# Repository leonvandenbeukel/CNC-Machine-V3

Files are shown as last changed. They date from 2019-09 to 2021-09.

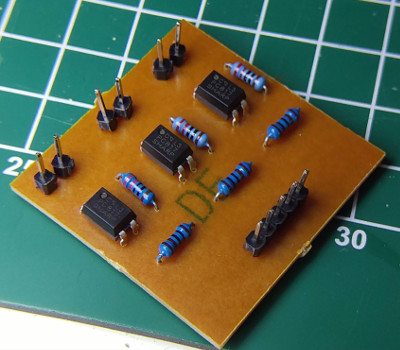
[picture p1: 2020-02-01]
Image/pcb3.jpg

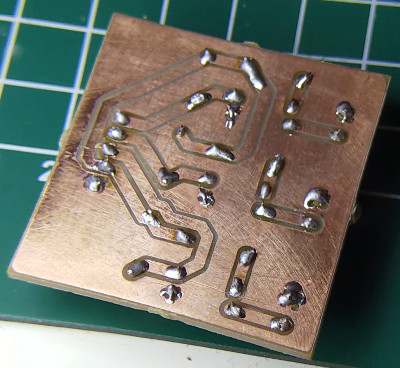
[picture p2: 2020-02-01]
Image/pcb2.jpg

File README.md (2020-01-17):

# CNC Machine V3
 
### Warning and disclaimer

Just as mentioned with my previous version, if you want to build this machine yourself you can download all the necessary files but I don't have enough time to give you much support so build it at your own risk! Also always be very careful with powertools, and only use them if you know what you're doing. 

### Wiki

Check out the [Wiki](https://github.com/leonvandenbeukel/CNC-Machine-V3/wiki) for specific milling info and parameter settings.

### License

<br />This work is licensed under a <a rel="license" href="http://creativecommons.org/licenses/by-nc-sa/4.0/">Creative Commons Attribution-NonCommercial-ShareAlike 4.0 International License</a>.

If you have any suggestions on how to make the machine better, please let me know!

### Introduction
 
This is a modified version of my previous homemade CNC machine. Instead of using threaded rods this one uses (GT2) belts and has a larger working area of 50x70 cm or 20x27 inch. By using belts it's also faster. I'm also using microstepping now (all three jumpers) on the Arduino CNC shield. The STL files for 3D printing can be found in the STL folder. 

The metal tubes are 20x20mm and approx. 1 meter long (X axis is a little shorter). 

### Design

I've designed the 3D printed parts with Fusion 360 and used Inkscape for the Y axis drilling template. To control the machine I'm using an Arduino UNO with GRBL firmware and an Arduino CNC Shield. There are plenty of tutorials to find on how to connect and use it so I did not show it in the video. Here are some useful links:

* [GRBL](https://github.com/gnea/grbl)
* [Arduino CNC Shield](https://blog.protoneer.co.nz/arduino-cnc-shield/)

### 3D Printing

The 3D printer I use is an Anet A8. The parts are printed with PLA, mostly 20% infill and 0.2 or 0.4 setting. Use higher infill for parts that must be stronger, for example the stepper motor mounts.

| 3D Printed components | x Print |
| --- | ----- |
|Bearing Belt Guidener | 6x |
|Router Mount | 1x |
|Universal Mount | 4x |
|X Axis Belt Holder | 4x |
|X Axis Motor Mount | 1x |
|X Axis Sidepanel Mount Inside  | 2x |
|X Axis Sidepanel Mount Outside | 2x |
|X Axis Spacer | 2x |
|Y Axis Motor Mount and Slider  | 2x |
|Y Mount | 4x |
|Z Axis Bottom Front | 1x |
|Z Axis Top Front | 1x |
|Z Carriage Back | 1x |
|Z Carriage Top | 1x |
|Z Motor Mount | 1x |
|Z Slider Bottom | 1x |
|Z Slider Top | 1x |
|Z Spacer | 1x |

### Dimensions

The tubes are 20mm x 20mm (0.78") square steel tubes. The length of the Y Axis tubes is 1000mm (40") and the length for the X Axis is approx. 820mm (32"). As an alternative you could also use other dimensions than 20mm x 20mm (maybe even rounded tubes) as long as they are approximately that size. The Z axis tubes are 15mm x 15mm (0.59") aluminium square tubes, approx. 215mm long (8.5"). You should measure this for yourself, check the video build. For the belts I'm using GT2 6mm and pulleys.

The effective working area is 50 x 70 cm (20" x 27").

### Power and motors

To power the NEMA 17 stepper motors I've converted an old ATX PC power supply and used the 12V output. The type of stepper motors I use for the Y- and Z axis are: 17HS19-2004S1, the type for the X axis is: 42BYGHW811. Both type of motors can be used. For the wiring I've used CAT5 network cable.

### Cost Estimation

* [Link to Google Sheet](https://docs.google.com/spreadsheets/d/1WaLTZEe9Un130kNA_mwn08Lo0E_RAs8ju6dJp0eKexQ/edit?usp=sharing "Link to Google Sheet")

### Router 

I'm using a Makita M3700 router but you can use any router that has an approx. diameter of 65mm (2.5"). Or you might have to design another router mount or create an adapter.

### YouTube video

<a href="https://youtu.be/PrJPGO_sYMM" target="_blank">Click to view: 3D Printed CNC Machine V3</a>

### Software that I mostly use to generate and send GCode:

* bCNC (https://github.com/vlachoudis/bCNC)
* Universal Gcode Sender (https://github.com/winder/Universal-G-Code-Sender)
* Easel by Inventables (http://easel.inventables.com)
* Fusion 360 with Design and Manufacturing mode (https://www.autodesk.com/products/fusion-360/students-teachers-educators)

### GRBL

I've made some changes to the GRBL config.h file before flashing it to the Arduino. The changes are not mandatory but helps if you are using (hard) limit switches. The changes I've made in the config.h file are as follows (check the [GRBL](https://github.com/gnea/grbl) page for more info):

```
// Line 88: I've disabled the initial lock because it's just annoying :) 
// #define HOMING_INIT_LOCK

...

// Line 105: I wanted the homing cycle to first home Z than X and then Y (default it homes X and Y simultaneously)
#define HOMING_CYCLE_0 (1<<Z_AXIS)                // REQUIRED: First move Z to clear workspace.
#define HOMING_CYCLE_1 (1<<X_AXIS)                // Then home X
#define HOMING_CYCLE_2 (1<<Y_AXIS)                // Then home Y

...

// Line 342: I commented out this to enable homing for the Z axis again (swap pins D11 and D12 on Arduino).
// #define VARIABLE_SPINDLE // Default enabled. Comment to disable.

```

These are my GRBL machine settings. This might not work for you so check each setting carefully:

```
$0 = 10    (Step pulse time, microseconds)
$1 = 255    (Step idle delay, milliseconds)
$2 = 0    (Step pulse invert, mask)
$3 = 0    (Step direction invert, mask)
$4 = 0    (Invert step enable pin, boolean)
$5 = 0    (Invert limit pins, boolean)
$6 = 0    (Invert probe pin, boolean)
$10 = 3    (Status report options, mask)
$11 = 0.010    (Junction deviation, millimeters)
$12 = 0.002    (Arc tolerance, millimeters)
$13 = 0    (Report in inches, boolean)
$20 = 0    (Soft limits enable, boolean)
$21 = 0    (Hard limits enable, boolean)
$22 = 1    (Homing cycle enable, boolean)
$23 = 3    (Homing direction invert, mask)
$24 = 25.000    (Homing locate feed rate, mm/min)
$25 = 500.000    (Homing search seek rate, mm/min)
$26 = 100    (Homing switch debounce delay, milliseconds)
$27 = 1.000    (Homing switch pull-off distance, millimeters)
$30 = 1000    (Maximum spindle speed, RPM)
$31 = 0    (Minimum spindle speed, RPM)
$32 = 0    (Laser-mode enable, boolean)
$100 = 80.000    (X-axis travel resolution, step/mm)
$101 = 80.000    (Y-axis travel resolution, step/mm)
$102 = 500.000    (Z-axis travel resolution, step/mm)
$110 = 3000.000    (X-axis maximum rate, mm/min)
$111 = 3000.000    (Y-axis maximum rate, mm/min)
$112 = 3000.000    (Z-axis maximum rate, mm/min)
$120 = 10.000    (X-axis acceleration, mm/sec^2)
$121 = 10.000    (Y-axis acceleration, mm/sec^2)
$122 = 10.000    (Z-axis acceleration, mm/sec^2)
$130 = 400.000    (X-axis maximum travel, millimeters)
$131 = 200.000    (Y-axis maximum travel, millimeters)
$132 = 200.000    (Z-axis maximum travel, millimeters)
```

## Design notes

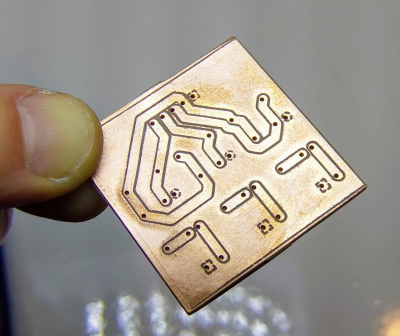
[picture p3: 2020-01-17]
Image/pcb.jpg

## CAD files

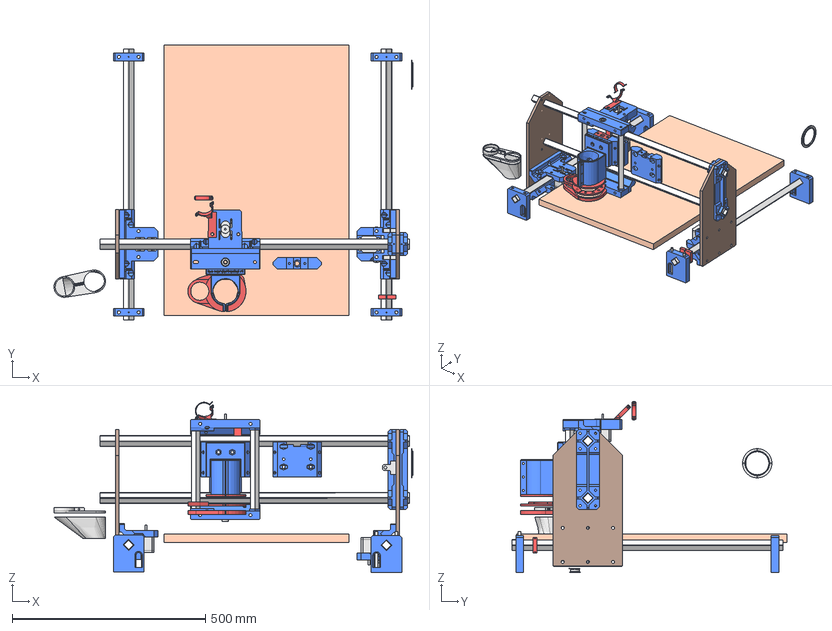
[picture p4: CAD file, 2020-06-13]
Model/CNC Machine V3.FCStd
927.8 x 711.0 x 442.3 mm
Z Rails Right
Z Rails Left
Z Motor
Y Universal Mount Left Bottom
X Rails Bottom
Y Motor Left Bottom Down
Y Axis Motor Mount and Slider Top Left
Z Universal Mount Bottom
X Rails Top
Y Rails Left
X Motor
Y Rails Right
Y Motor
Z Universal Mount Top
X Axis Belt Holder Left
Bearing X Right
Bearing Y Right
Bearing Y Left
Bearing X Left
Bearing Z
Y Rod Left
Y Rod Right
Panel Left
Y Mount Front Left
Y Mount Back Left
Y Mount Back Right
X Axis Sidepanel Mount Inside
X Axis Sidepanel Mount Outside
X Axis Motor Mount
Y Mount
Y Axis Motor Mount and Slider
Z Carriage Back
Z Carriage Top
Z Motor Mount
Z Axis Top Front
Z Axis Bottom Front
Z Spacer
X Axis Belt Holder
Z Slider Top
Router Mount
Z Slider Bottom
Router Magnet Holder
Dust Collector Top Part
Dust Collector Bottom Part
Hose clamp Bottom 45 degr
Hose clamp Top
X Axis Sidepanel
Universal Mount
Bearing Belt Guidener
End Stop 2
End Stop 1
Z End Stop
Z Carriage Back 52mm spindle
Vacuum hose adapter
Wasteboard
Dust Collector top
Dust Collector bottom

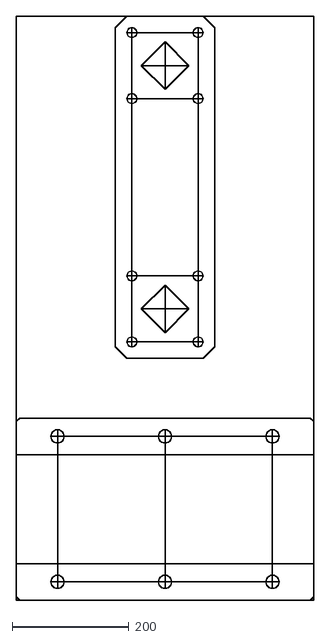
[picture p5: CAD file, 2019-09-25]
Sidepanel template.dxf
510.2 x 1001.5

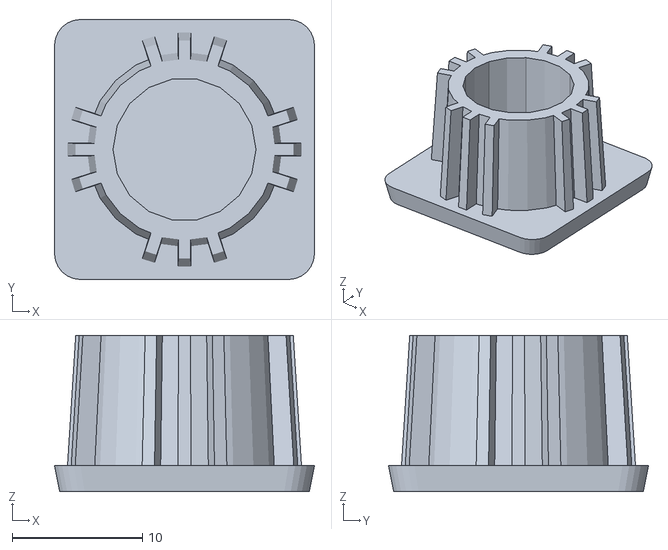
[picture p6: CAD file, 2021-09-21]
STL/endcap.stl
20.0 x 20.0 x 12.0

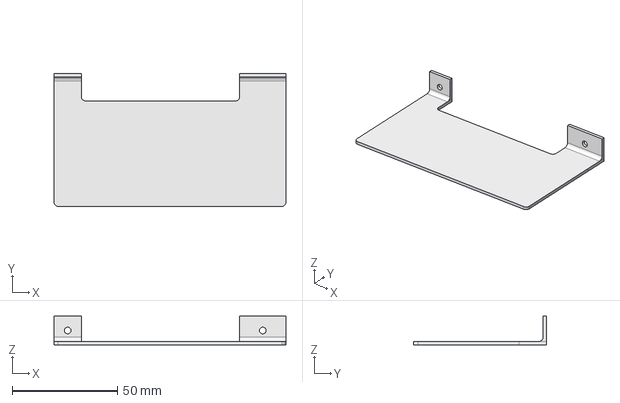
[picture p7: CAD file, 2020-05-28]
Model/Power supply lid.FCStd
110.0 x 63.0 x 13.6 mm

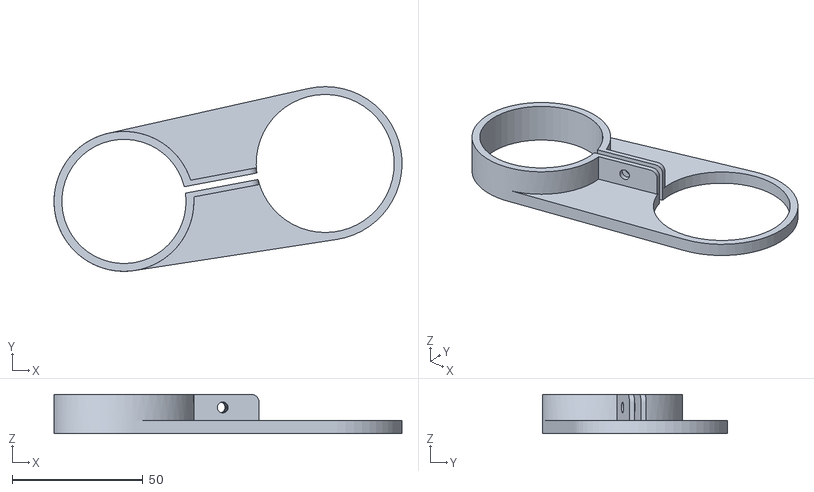
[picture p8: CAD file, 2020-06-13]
STL/Dust Collector Top Part - 52mm 500W spindle.stl
133.1 x 70.7 x 15.0

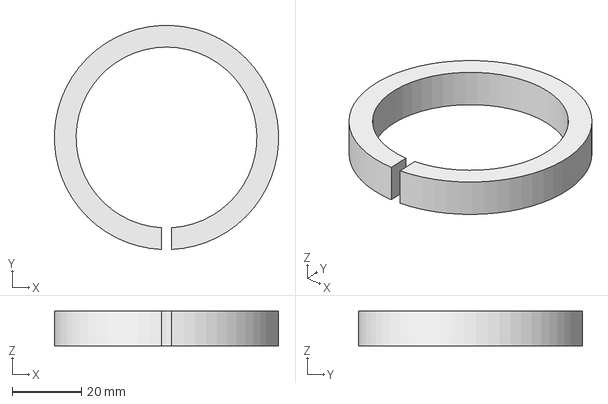
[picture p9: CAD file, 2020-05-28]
Model/Spindle Motor Adapter.FCStd
64.9 x 64.9 x 10.0 mm

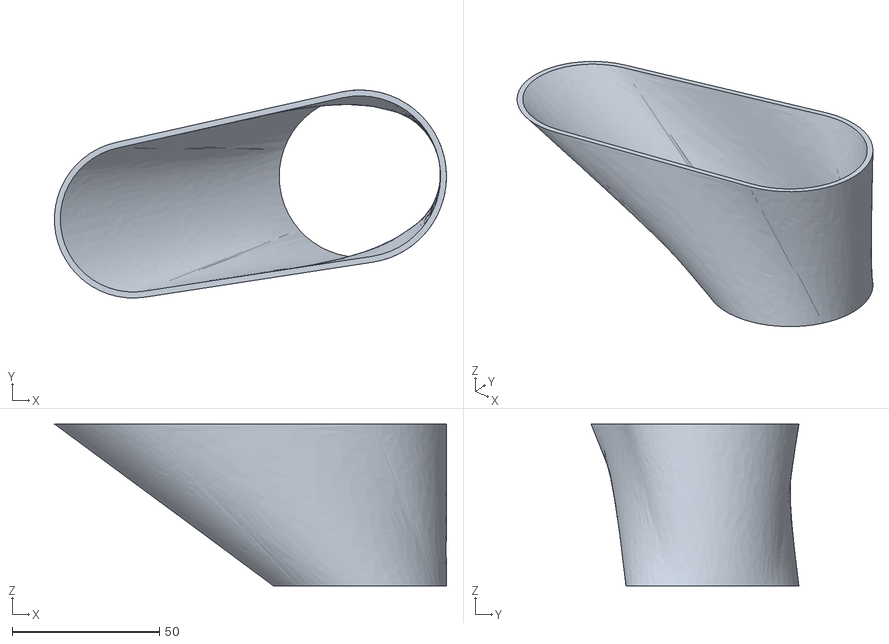
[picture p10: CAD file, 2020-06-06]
STL/Dust Collector Bottom Part - 52mm 500W spindle.stl
133.1 x 70.6 x 55.0

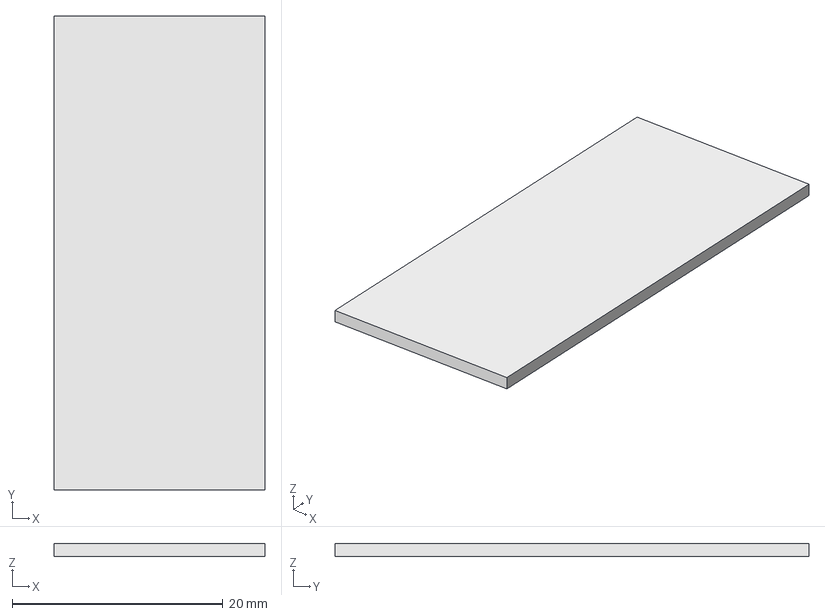
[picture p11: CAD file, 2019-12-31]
Model/Z End Stop Helper.FCStd
20.0 x 45.0 x 1.20 mm

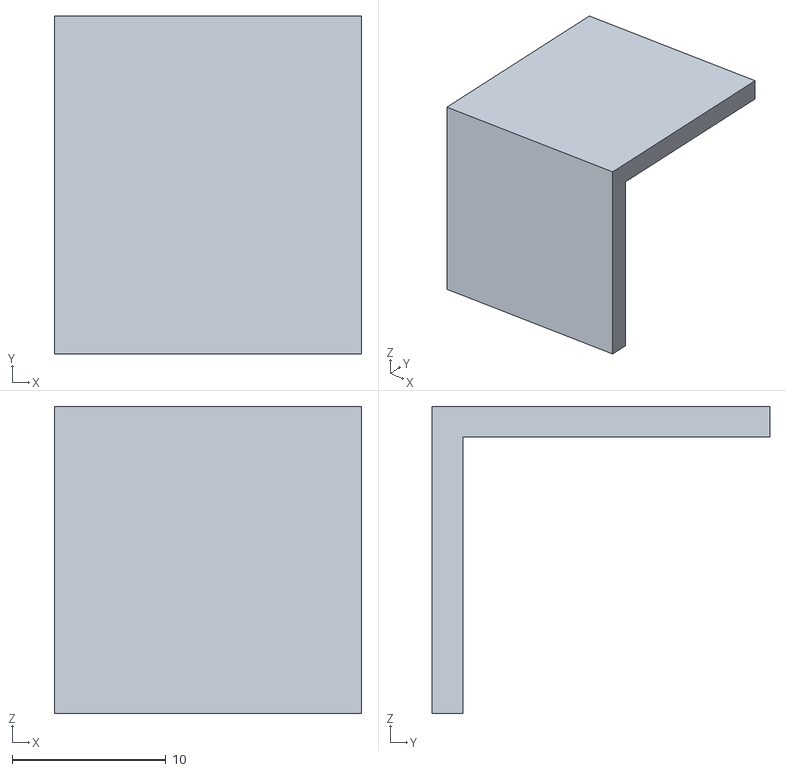
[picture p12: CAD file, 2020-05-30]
STL/Z End Stop.stl
20.0 x 22.0 x 20.0

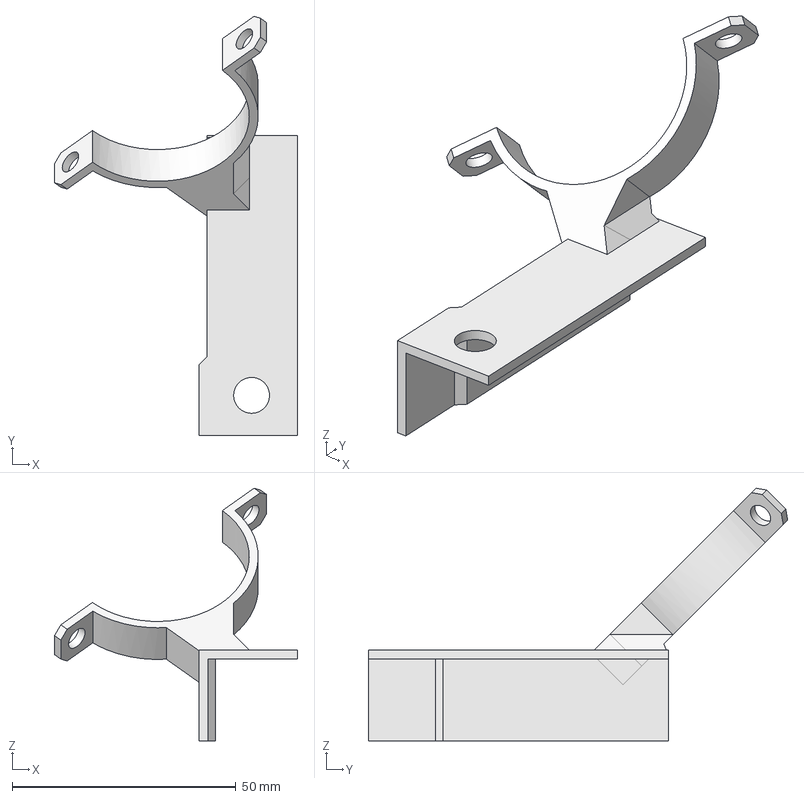
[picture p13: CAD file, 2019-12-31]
Model/Hose clamp Bottom 45 degr.FCStd
54.2 x 93.6 x 56.4 mm

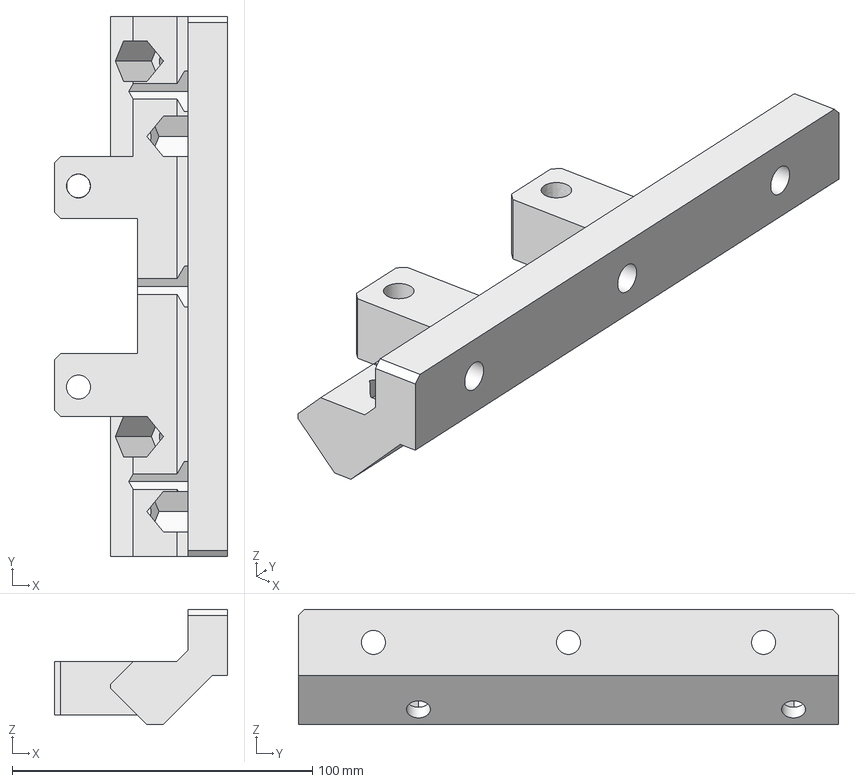
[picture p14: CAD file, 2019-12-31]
Model/Universal Mount.FCStd
57.6 x 180.0 x 38.4 mm

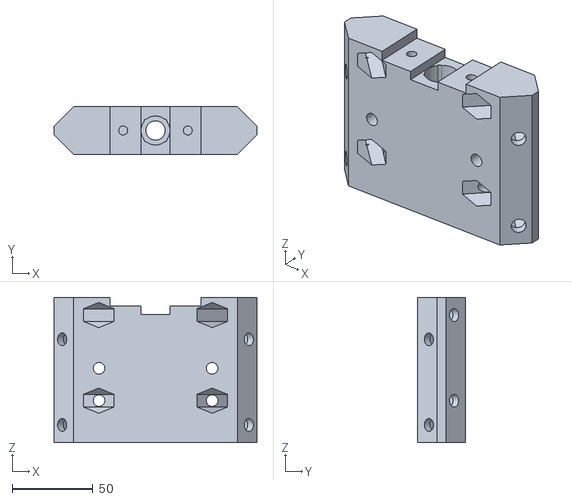
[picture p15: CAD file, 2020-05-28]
STL/Z Carriage Back - spindle 2.stl
125.7 x 29.7 x 90.0

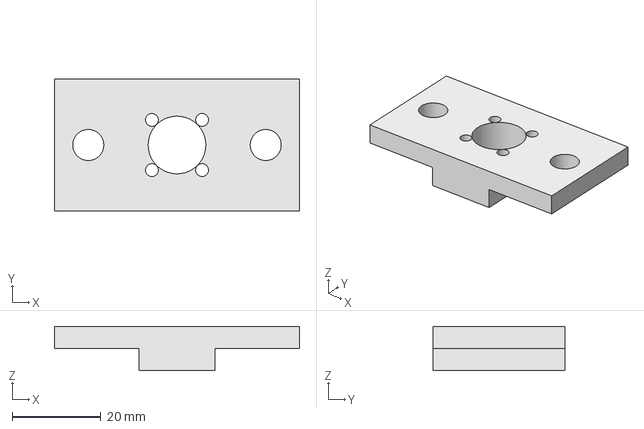
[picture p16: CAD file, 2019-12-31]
Model/Z Carriage Top.FCStd
55.2 x 29.7 x 10.0 mm

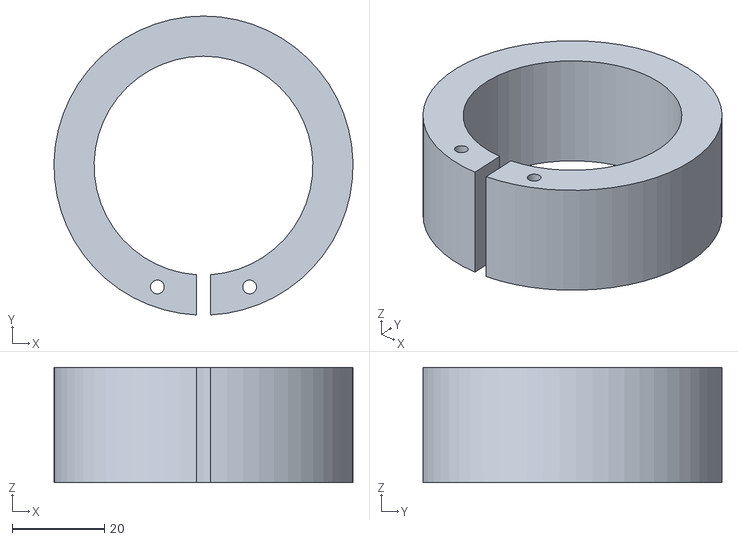
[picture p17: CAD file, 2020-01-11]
STL/Dremel Adapter.stl
64.8 x 64.8 x 25.0

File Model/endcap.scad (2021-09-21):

// Endcap for 20mm square steel tubing
// Designed for Leon CNC by Peter Hertel 2021
// CC-BY 4.0 license

// Variables

od = 20; // [20] outer diameter of square tubing
id = 18; // [18] inner diameter of square tubing, adjust this if fit is too tight
offset = 2; // [2] amount of rounded corners
tab_size = 3; // [3] depth/length of tabs 
tab_width = 1; // [1] width of tabs

// The end cap itself
    mirror([0,0,1]) // mirrored to get the chamfer on the bottom/outside
    linear_extrude(height=2,scale=0.96) // extrusion of the 2D shape defined below, scaled to chamfer the edge
    offset(offset,$fn=24) // restores the basic shape to its original od size, rounding the corners in the process
    offset(-offset) // makes the basic shape smaller
        square(od,center=true); // basic 2D shape of end cap, modified above

// Internal shape
// Made spiky with tabs to conform to inside burr after cutting
// Might need slight convincing with a mallet to fit snugly

difference(){ // making the center hollow
    linear_extrude(height=10,scale=0.93){ // makes the 3D shape with a slight scale/chamfer along the edge for easier insertion
        circle(r=id/2-tab_size/2); // basic shape of center cylinder
        for(Y=[90:90:360]) // makes four of the shapes below
            for(X=[-1:1]) // makes three of the shapes below
                rotate([0,0,360/20*X+Y]) // rotates the tabs around the center
                translate([0,-tab_width/2]) // moves the tab to center
                    square([id/2,tab_width]); // basic shape of tab
}
cylinder(r=id/2-3.5,h=20); // basic shape of center hole
}

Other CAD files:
STL/Spinle Motor Adapter.stl
Model/Bearing Belt Guidener.FCStd
STL/Grinder Adapter.stl
Model/Y Mount.FCStd
Model/Dust Collector Bottom Part.FCStd
Model/Dust Collector Top Part.FCStd
Model/End Stop.FCStd
Model/Hose clamp Top.FCStd
Model/Router Magnet Holder.FCStd
Model/Router Mount.FCStd
Model/Vacuum hose adapter.FCStd
Model/Wasteboard.FCStd
Model/X Axis Belt Holder.FCStd
Model/X Axis Motor Mount.FCStd
Model/X Axis Sidepanel Mount Inside.FCStd
Model/X Axis Sidepanel Mount Outside.FCStd
Model/X Axis Sidepanel.FCStd
Model/Y Axis Motor Mount and Slider.FCStd
Model/Z Axis Bottom Front.FCStd
Model/Z Axis Top Front.FCStd
Model/Z Carriage Back.FCStd
Model/Z Motor Mount.FCStd
Model/Z Slider Bottom.FCStd
Model/Z Slider Top.FCStd
Model/Z Spacer.FCStd
STL/Bearing Belt Guidener.stl
STL/Dust Collector Bottom Part.stl
STL/Dust Collector Top Part.stl
STL/End Stop Left.stl
STL/End Stop Right.stl
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

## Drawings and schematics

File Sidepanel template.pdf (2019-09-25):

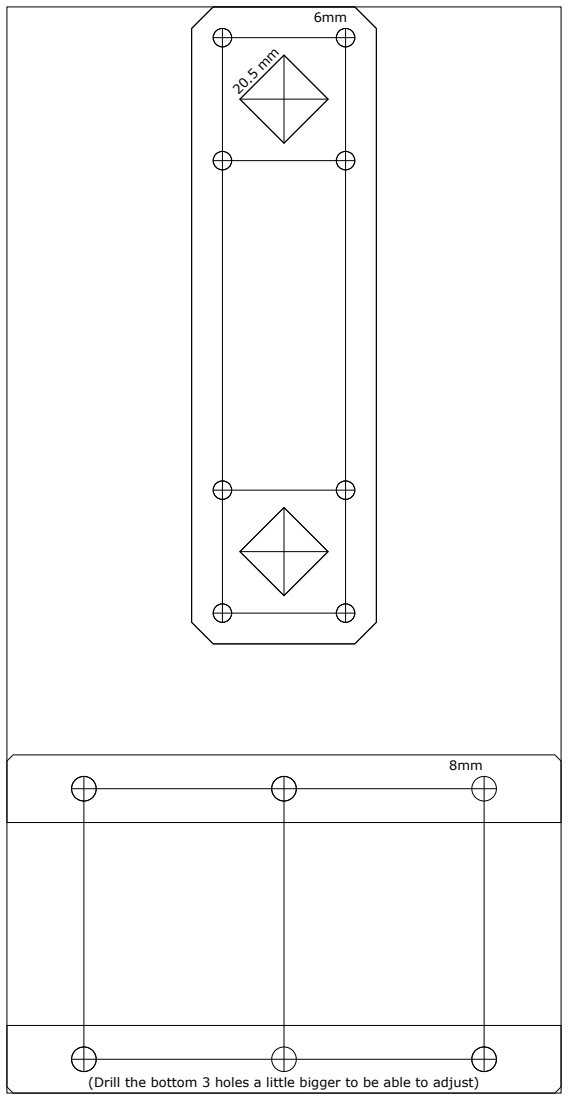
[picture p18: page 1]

(Drill the bottom 3 holes a little bigger to be able to adjust)

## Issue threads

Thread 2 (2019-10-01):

Question: Which screws sizes and lengths are needed!

Multi94, 2019-10-01:
Hi,
I have a question about the cnc but in advance the router I like very well and I have decided to convert my Mpcnc to a router of its type. Unfortunately, I do not know what screws I need for it I would not necessarily buy half the hardware store to find the right screws. Could you maybe say something more specific so I can buy these screws then.

Thanks for your efforts.

bigbass1997, 2019-10-05:
@Multi94 You can open the STL files into a CAD editor, such as Fusion 360, and use the inspect tool to check the sizes of each hole. From my peek at some of the files, it seems it uses primarily M6 (6mm) and M8 (8mm) sized holes.

Closed 2019-11-02.

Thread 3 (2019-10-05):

Fusion 360 or STEP files

bigbass1997, 2019-10-05:
Even though STL files are adequate for 3D printing, I'd really appreciate if there was an easier way to view and edit the parts. I've noticed that you use Fusion 360 for the design work, and if you're okay with it, I think it would be a great help for everyone if you could either share a Fusion 360 public link for the project (preferable option), or alternatively export STEP files for each part.

STL files are just approximations of the original design, made up of many triangles. There's no feature history or any truly curved surface. Working with them is honestly really difficult, beyond just sticking them into a slicer program.

If you're not sure how to share a Fusion 360 design, there are instructions on [the Autodesk website](https://knowledge.autodesk.com/support/fusion-360/troubleshooting/caas/sfdcarticles/sfdcarticles/How-to-share-a-Fusion-360-design.html). (Of course, the CC BY-NC-SA license these models are protected under, would still be followed. In case you're worried about that.)

I'm planning to make a CNC machine using your design, and this improved accessibility to the design would greatly help me and I bet others would appreciate it too.

reefwarrior, 2019-10-13:
It would be greatly appreciated if this will be possible? :)

nunoadferreira, 2019-11-04:
Hi,

Thanks for sharing this great project. I loved it and I will definitely build one for myself. However, I have a prusa mini which can only print an area of 180 x 180 mm and the side panels are bigger than that. So I am thinking in splitting them to print in two pieces. It would be so useful if you could share the fusion 3d files or just the step files.

leonvandenbeukel, 2020-01-02:
The design is now available as a FreeCAD model (check the model folder).

Closed 2020-01-02.

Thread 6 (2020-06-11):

Some Questions to Machine v3

rainerschulte, 2020-06-11:
Hi, I'm currently building the CNC V3 and found some Issues.

1. The belts on Y-Axis cannot be adjusted, when fully assambled the X/Y-Axis because the Steppers are not raechable from below.
2. The Z-Axis Motor touches the upper rail when Using the 30 Teeth Pulleys.
3. The most important Issue is selfmade. I built the mechanics on my Modeling Workbench with 1800 x 600 mm and the Steel-Rails are bending a bit. I'm affraid (or pretty shure) that it becomes worse when adding Dust collection. Any Idea how to fix this?

Petesystemspecialist, 2020-07-26:
Part of the Y mount STL file is missing!. Its the smaller slider

rainerschulte, 2020-07-28:
>
>
> Re CNC ver 3 . one of the 3 Y mount STL files is missing!. The Smaller slider is not shown. I'm stuck without it.

It's the "Universal Mount". It`s not labled seperately. These days my new Makita Router will arrive. I found my old little Dremel with the small Bits not being rigid enogh. I will test some new Collars from DREMEL for fine work.
Funny... I like it, when it moves! Now I need to find out to find out how to change Tools in bCNC. Until here I'm happy with my CNC.

Petesystemspecialist, 2020-07-28:
Hi there

& thankyou for your help. Its a pity there are no images attached to the
parts.
Anyway, the 3d printer is hard at work again.
I like your comments re the Dremel. I was going to use this, but in view of
your comments,  I will get the larger ( Chinese copy :(
Best wishes

Peter Ford

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

Nudel, 2020-10-04:
>     3. The most important Issue is selfmade. I built the mechanics on my Modeling Workbench with 1800 x 600 mm and the Steel-Rails are bending a bit. I'm affraid (or pretty shure) that it becomes worse when adding Dust collection. Any Idea how to fix this?

I found some interesting discussions here: https://www.model-engineer.co.uk/forums/postings.asp?th=107717

My take is you could either get a thicker walled rail or hammer in a round rail to stiffen it up.

I would also consider filling it with concrete (or epoxy?), but I haven't had the time to find any definite answers if it would help that much.

The third option would require a redesign of the y axis motor mount. If you moved the motor to the opposite side of the x axis sidepanel you might be able to fit a support foot between the runners on the y axis rails. Just an idea.

> Hi there & thankyou for your help. Its a pity there are no images attached to the parts.
If you open the whole model in freecad you can select the individual parts to find the name for it, or select the component name and have it highlighted on the model. Maybe that could help a bit?

rainerschulte, 2020-10-04:
After some tries to mill something I decided to switch to a complete other Design. I had several Issues with Belt tensioning and found it very unpracticable to reach the Motors between Table and Mounts. My new CNC has much more build area and all Motors can be accessed without hassle. I have now 1000 x 430 mm available and I get usable outcome.
Sorry Leon.. But it was a good practice to learn.

Closed 2020-10-04.

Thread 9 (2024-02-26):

Z axis rises a few millimeters on my cnc

SebSts69, 2024-02-26:
Hello, I love your work. I built a cnc based on the V3 model. It works very well and your 3D design is great. I would like to share a malfunction on the Z axis on my cnc. I don't know if I'm the only one who has it or if you already have it. This could also be an editing problem on my part. Indeed, the Z axis (the threaded rod) sometimes rises a few millimeters when the cutter does not fit sufficiently into the wood, which makes engraving or cutting ineffective. Have you ever had this problem? Did you solve it? There is in fact no anti-return system for the threaded rod at the pulley level on the z axis. everything stays in place just by weight? Thanks for your help

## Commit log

2019-09-30 Comment about motor type
2019-10-05 Added CNC machine dust shoe files
    [Dust Collector Bottom Part.stl, Dust Collector Top Part.stl, Hose clamp Bottom 45 degr.stl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]
2019-10-05 Added top clamp
    [Hose clamp Top.stl]
2019-12-31 Added FreeCAD model and end stops
    [Bearing Belt Guidener.FCStd, CNC Machine V3.FCStd, Dust Collector Bottom Part.FCStd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]
2019-12-31 Added z end stop helper
    [Z End Stop Helper.FCStd, Z End Stop Helper.stl]
2020-01-03 Merged end stops
    [CNC Machine V3.FCStd]
2020-01-04 Changed Z gear so $102 changed to 500 steps/mm
2020-01-11 Added an adapter for a mini grinder - print 2x
    [Grinder Adapter.stl]
2020-01-11 Mini grinder adapter
    [CNC Machine V3.FCStd]
2020-01-11 Added Dremel Adapter
    [CNC Machine V3.FCStd, Dremel Adapter.stl]
2020-01-17 Added pcb image
2020-05-28 Added mount for different spindle motor
    [CNC Machine V3.FCStd, Power supply lid.FCStd, Power supply lid.stl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]
2020-05-30 Added Z end stop clip
    [CNC Machine V3.FCStd, Z End Stop.stl]
2020-06-06 Dust collector for 52mm 500W spindle
    [CNC Machine V3.FCStd, Dust Collector Bottom Part - 52mm 500W spindle.stl, Dust Collector Top Part - 52mm 500W spindle.stl]
2020-06-13 Added dust collector for 500W 52mm spindle and surface gcode
    [CNC Machine V3.FCStd, Dust Collector Top Part - 52mm 500W spindle.stl, Vacuum hose adapter.stl]
2021-09-19 Added a simple end cap
    See .scad file for detailed comments
    [endcap.stl]
2021-09-19 Added a simple end cap
    Se file for detailed description
    [endcap.scad]
